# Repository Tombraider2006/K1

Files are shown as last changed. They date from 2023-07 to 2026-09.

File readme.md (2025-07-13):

<h3 align="right"><a href="https://www.tinkoff.ru/rm/yakovleva.irina203/51ZSr71845" target="_blank">ваше "спасибо" автору</a></h3>
<h3 align="right"><a href="https://t.me/tombraider2006" target="_blank">телеграм канал автора</a></h3>

[**Обучение в режиме онлайн консультации**](kurs.md)

[**дополнительные материалы к лекциям**](/extras/readme.md)

<h5 align="right">поставьте "звездочку" проекту. так другим пользователям легче его найти.</h5>

<h2>А я вам сейчас покажу откуда...</h2>

[**Актуальная версия прошивки с инструкциями по установке**](/version_config/readme.md) начинайте читать отсюда.

[**Обзор и быстрый старт прошивки Simple Af.**](/version_config/SimpleAF.md) Продвинутый вариант прошивки, Для этого варианта необходимо докупить датчик по Z.

[**Разное полезное про меню Helper Script**](/random/menu.md) то чего не написали нигде...

[**Родные коды ошибок креалити K1C**](https://store.creality.com/blogs/all/creality-k1c-fault-codes) по мне бесполезная шляпа, гораздо правильнее читать сообщения от клиппера в вебпанели. но если очень хочется можно и почитать. 

[**Родные коды ошибок креалити K1MAX**](https://store.creality.com/blogs/all/creality-k1-max-fault-codes-list) по мне бесполезная шляпа, гораздо правильнее читать сообщения от клиппера в вебпанели. но если очень хочется можно и почитать. 

[**Читаем графики шейперов**](/shaper/readme.md) Быстро разбираемся с графиками шейперов.

[**Регулировка натяжения ремней опираясь на графики**](/random/belts/readme.md) Разбираемся с графиком натяжения ремней, не быстро...

<h2>Макросы</h2>

[**Полезные макросы**](/macros_helpfull/readme.md) упрощаем работу с макросами формируя отдельный раздел с теми которыми будем пользоваться.

[**Управляем ретрактом во время печати**](/retract/readme.md) На коленке сляпанная инструкция далеко не всем нужная. 

[**Еще несколько советов по принтеру**](/ferma/readme.md) Разные полезные мелочи которые могут быть полезны при организации процесса печати.

[**таймер отложенной печати**](/random/timer.md) частный случай, однако пока его делал  нашел один интересный файлик который потом стал частью хелпер скрипта. 

[**Пропуск самопроверки после сброса до заводских настроек**](/random/reset.md)

<h2>Моды</h2>

[**Что купить чтобы принтер вас любил**](/what_2_buy/readme.md) статья в процессе правок

[**Актуальные печатные модификации**](https://t.me/crealityK1rus/16778) так как все течет все меняется, самые актуальные модели в телеграмм группе. 

[**Замена сопла Unicorn на Volcano в Creality K1\k1c\k1max**](https://3dtoday.ru/blogs/dimix200612/zamena-sopla-unicorn-na-volcano-v-creality-k1) при печати твердыми пластиками вполне неплохой выход удешевления затрат на сопла.

[**Установка стекла на стол для исправления кривизны**](https://www.youtube.com/watch?v=6vU0u630IjU&t=867s&ab_channel=ZeroDotCMD) видео на ютубе от зарубежного блогера, автоперевод субтитров вам в помощь 

[**Как поправить исправить наклон стола быстро**](https://www.youtube.com/watch?v=S2d_9Ysz-Q8&ab_channel=ZeroDotCMD) видео на ютубе от зарубежного блогера, автоперевод субтитров вам в помощь 

<h2>ОчУмелые Ручки</h2> Моды не всем нужные и на свой страх и риск.

[**Зачем нам одноплатник?**](/random/pi.md) различные модули которые не могут встать на родную операционную систему однако можно поставить на сторонний сервер **Spoolman**, **Telegram Bot**, **Klipperscreen**

<details><summary> <b>Активная термокамера. Cборник мануалов</b> </summary>

1. [**Подключение нагревателя камеры принтера**](/random/heater_chamber/readme.md) Если вы печатаете АBC и им подобными пластиками вам это пригодится.

2. [**Установка активного нагревателя термокамеры**](https://docs.idryer.org/iHeater/README_ru/) универсальнее стороннее решение с легкой установкой в любой принтер на клиппер.

3. [**Продвинутый вариант термокамеры с использованием дополнительного mcu**](https://github.com/artem-sedykh/K1C-chamber-heater)

</details>

<p>

[**Установка хотенда от Creality K2 Plus на Creality K1/c/max/se**](https://telegra.ph/Ustanovka-hotenda-ot-Creality-K2-Plus-na-Creality-K1cmaxse-05-13-2) Установка хотенда от K2 может понадобиться, если вы хотите увеличить максимальный объёмный расход на вашем принтере.

[**Подключение Raspberry Pico для расширения количества pin для ваших самоделок и дополнений**](/usb/readme.md) также добавил несколько примеров использования например для того же SFS

[**Датчик филамента sfs 2.0 для k1c\k1\k1max**](/sfs/readme.md) когда у нас не просто датчик обрыва филамента, а еще с реакцией если филамент остановился. пробка\запутывание филамента\окончание катушки с загнутым филаментом.

[**FBP Mod**](https://github.com/tlace17/K1-Flanged-Bearing-Project) замена стоковых деталей портала на напечатанные. есть свои плюсы, но свою пряморукость нужно учитывать до старта работы над проектом.

[**Установка сетевого разъема RJ45 на К1\K1C**](/random/ethernet.md) требует навыков пайки. 

[**Руководство по установке WLED**](https://github.com/Gliptopolis/WLED_Klipper) если очень хочется сделать из принтера новогоднюю ёлку.

[**Описание custom_macro.py**](/random/custom_macro.md) когда купил к1 думая что там обычный и клиппер и теперь сидишь и ничего не понимаешь.

[**Распиновка плат принтера**](https://docs.google.com/presentation/d/1f6kJbMq7uSggC33zmIfcTPdG6r50PbbDut14u9vAcZA/edit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) Энтузиастам.

[**выбор самурая - переход на клиппер без креалити**](https://github.com/pellcorp/creality/wiki/K1-Stock-Mainboard-Less-Creality)

[**Cartographer 3D. Если переходить на чистый клиппер придется уходить с родного модуля тензодатчиков.**](https://docs.cartographer3d.com/cartographer-probe/installation-and-setup/creality-k1-and-k1-max-specific)

[**Установка Creality K1 BTT Eddy**](https://ballaswag.github.io/blog/creality-k1-btt-eddy-guide/) буду ставить себе.. потом распишу подробнее.

[**модель держателя BTT Eddy с соединением в разьем лидара**](https://www.printables.com/model/1040464-btteddy-creality-k1-k1c-k1-max-mount)

[**Подключение одноплатника OrangePi (или любого другого) к K1.**](https://github.com/Lukich86/K1-host-conversion)

[**выбор самурая - ставим другую материнку, на примере MANTA 8**](https://docs.google.com/document/d/1aXhsg2oq-k43R_2uWEkFxx4bUmE72XdTxru3hAUbRM0/edit?tab=t.0)

[**обновленный тензомод**](https://github.com/Sekilsgs2/creality_pellcorp) где автоматизированный скрипт сам все поставит , очистит от хлама creality и поставит последний klipper  и можно юзать. Не как в tenso_mod - поставил и пол дня настраивай переделывай чтобы вообще хоть что то работало

[**Установка кулера модели от Пылесоса Roborock**](https://telegra.ph/Podklyuchenie-ventilyatora-Roborock-syaososa-k-3d-printeram-linejki-K1-06-06) Установка "Сяососа" может понадобиться, если вы часто печатаете Pla, Tpu и др. материалами, требующими активного охлаждения. Вентилятор Roborock может быстрее охлаждать слой, нежели улитка 5015 или 4020, что позволяет печатать быстрее на участках с маленькой площадью слоя 

[**Добавление функционала на основе virtual_pins на примере отключения вентиляторов в конце печати.**](/random/pins.md) исключительно как пример ну и тем кому это надо.(сами себе злобные буратино. я предупредил.)

[**CREALITY K1 FAQ перед первым включением.**](/random/before_use.md) **устарело** если вам попался этот пункт до того как вы вскрыли принтер вполне возможно что вы избежите перекоса стола

**как быстро определить какое сопло(unicorn\volcano) на вашем принтере**

если видно отверстие на радиаторе хотенда и болтик под шестигранник значит у вас vulcano, если радиатор без отверстий значит unicorn.

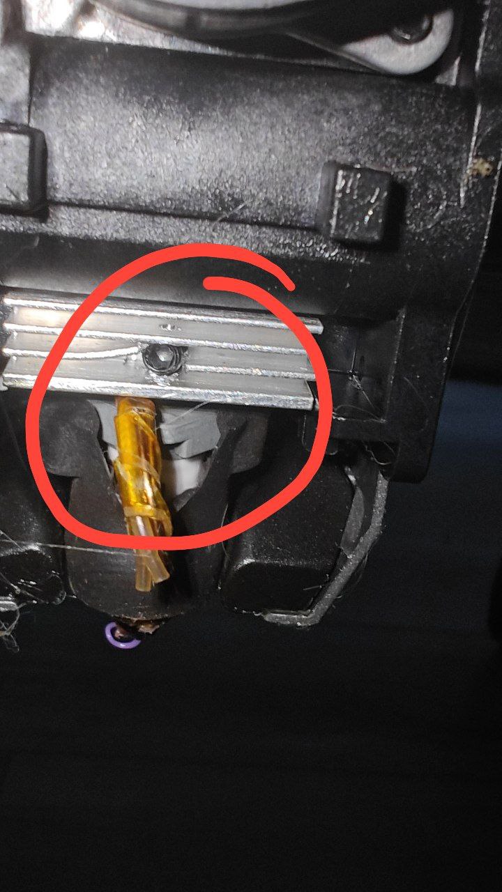
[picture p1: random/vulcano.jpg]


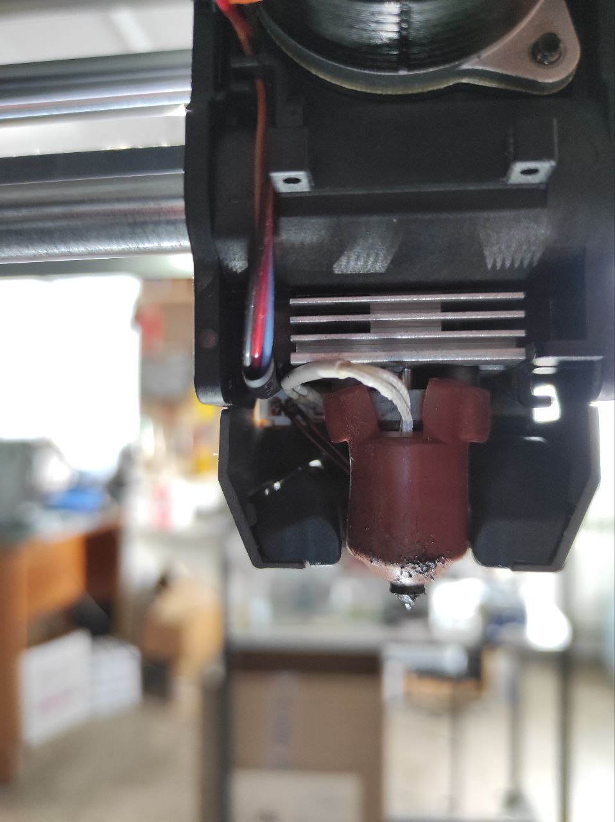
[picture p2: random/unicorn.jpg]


[**Ветка бутлоадера от CREALITY**](https://github.com/CrealityOfficial/K1_Series_Annex/releases/tag/V1.0.0)

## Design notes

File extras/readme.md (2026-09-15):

[↩️ Назад в главное меню](../readme.md)

---

# 📚 Дополнительные материалы к лекциям

> Полезные модели для печати, руководства по калибровке и видео-материалы

<h3 align="right"><a href="https://www.tinkoff.ru/rm/yakovleva.irina203/51ZSr71845" target="_blank">💝 Поддержать автора</a></h3>

---

## 📑 Оглавление

- [🔧 Печатные модели](#-печатные-модели)
- [🛠️ Устранение проблем со столом](#️-устранение-проблем-со-столом)
- [📊 Шейперы и калибровка](#-шейперы-и-калибровка)
- [🎯 Калибровка филамента](#-калибровка-филамента)
- [🎬 Видео-материалы](#-видео-материалы)
- [💧 Влажность пластика](#-влажность-пластика)
- [🛒 Расходные материалы](#-расходные-материалы)
- [⚙️ Adaptive PA](#️-adaptive-pa)

---

## 🔧 Печатные модели

### 1. Прокладка под экран

Уменьшает приток холодного воздуха в камеру принтера:

- **[K1 MAX](https://www.printables.com/model/553930-creality-k1-max-door-cover)**
- **[K1 / K1C](https://t.me/crealityK1rus/16778/293569)**

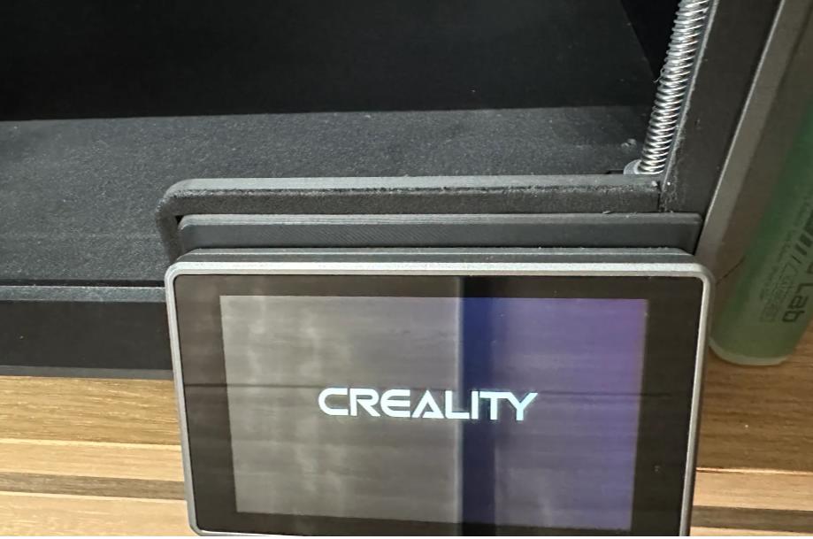
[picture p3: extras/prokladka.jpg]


### 2. Проставка для вентиляции

Устанавливается между корпусом и крышкой для улучшения воздухообмена:

- **[K1 / K1C](https://www.printables.com/model/525295-jc-creality-k1-hinged-lid-riser)**
- **[K1 MAX](https://t.me/crealityK1rus/16778/109114)**

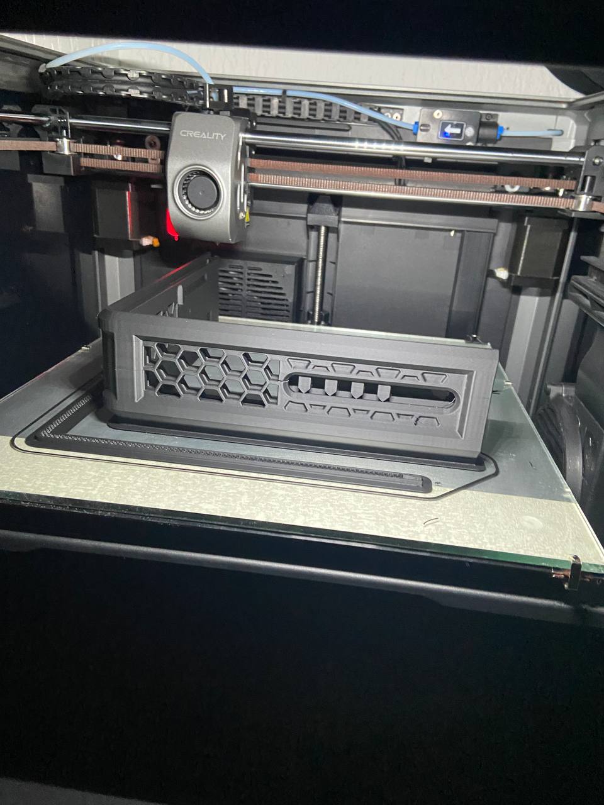
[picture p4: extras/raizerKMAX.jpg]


### 3. Держатель резинки прочистки

- **[Для K1C](https://t.me/crealityK1rus/16778/217607)**

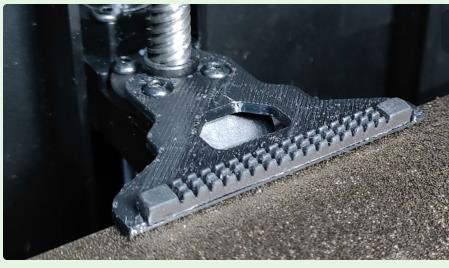
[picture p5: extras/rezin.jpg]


### 4. Тестовый кубик

**[Скачать обычный тестовый кубик](Cube.stl)**

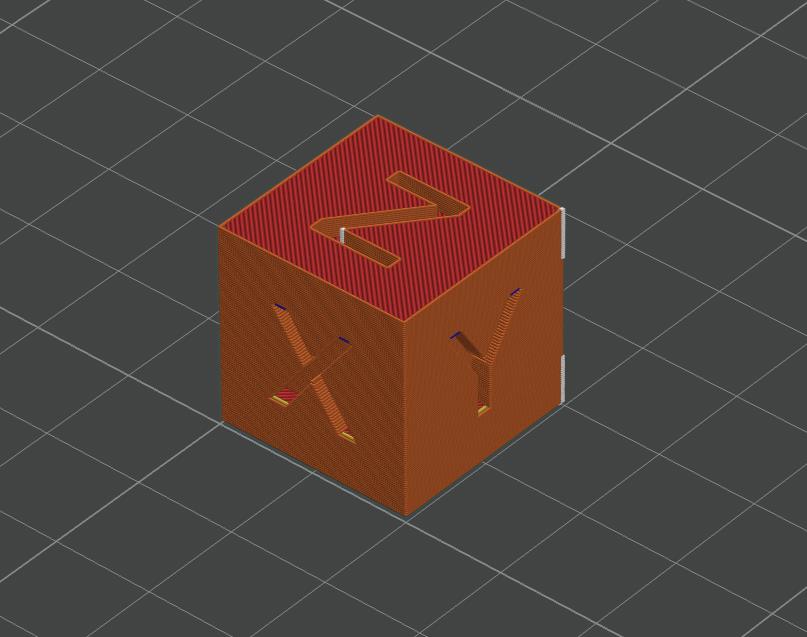
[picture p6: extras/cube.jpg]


---

## 🛠️ Устранение проблем со столом

### Методы исправления кривизны:

1. **[Установка стекла для исправления кривизны](https://www.youtube.com/watch?v=6vU0u630IjU&t=867s&ab_channel=ZeroDotCMD)** - видео на YouTube (англ.) | [Видео в чате K1](https://t.me/crealityK1rus/9504/602859)

2. **[Быстрое исправление наклона стола](https://www.youtube.com/watch?v=S2d_9Ysz-Q8&ab_channel=ZeroDotCMD)** - видео на YouTube (англ.)

3. **[Видеопояснение от пользователей](https://t.me/crealityK1rus/152020/451660)** - на русском в Telegram

---

## 📊 Шейперы и калибровка

### Что такое шейперы:

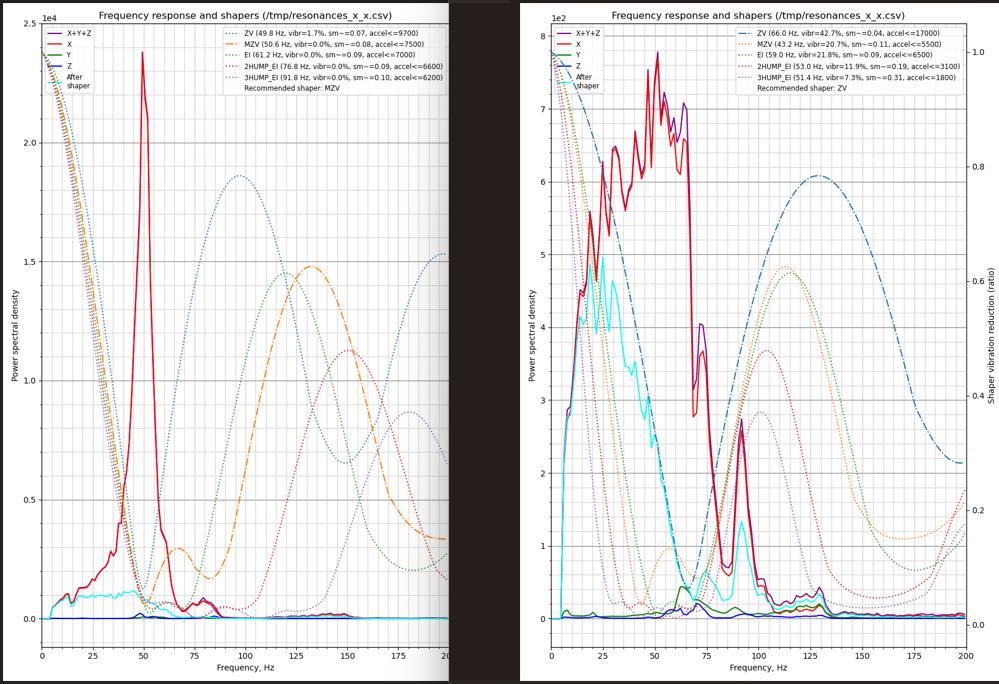
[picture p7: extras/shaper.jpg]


**Подробные материалы:**
- **[Материал на русском](https://github.com/Tombraider2006/klipperFB6/tree/main/accel_graph)** - подробная статья
- **[Материал на английском](https://github.com/Frix-x/klippain-shaketune/blob/main/docs/macros/axes_shaper_calibrations.md)** - от разработчиков
- **[Как понять графики шейперов](/shaper/readme.md)** - анализ графиков для K1 серии
- **[Регулировка натяжения ремней](/random/belts/readme.md)** - по графикам
- **[Helper Script меню](/random/menu.md)** - полезные функции

---

## 🎯 Калибровка филамента

### Порядок калибровки:

1. **Поток** (Экструзия)
2. **[Linear Advance](https://k3d.tech/calibrations/la/calibrator/)** (Pressure Advance)
3. **[Тест откатов](https://k3d.tech/calibrations/retractions/calibrator/)** (Retraction)
4. **Температура**
5. **Максимальная объемная скорость**

### G-коды для тестов Соркина:

⚠️ **Важно:** Используйте эти коды при калибровке PA и ретрактов

**Стартовый код:**
```gcode
_FULL_BED_MESH_ON
_ADAPTIVE_PURGE_LINE_OFF
START_PRINT EXTRUDER_TEMP=$HOTTEMP BED_TEMP=$BEDTEMP
```

**Конечный код:**
```gcode
SET_PIN PIN=FULL_BED_MESH VALUE=0
_ADAPTIVE_PURGE_LINE_ON
END_PRINT
```

---

## 🎬 Видео-материалы

### Слайсеры и настройка:

- **[Почему OrcaSlicer](https://youtu.be/0TzEFStKH90?si=3XKylqedC36pHxEK)** - обзор слайсера
- **[OrcaSlicer - Установка, Настройка, Работа](https://youtu.be/LeLj5oCacak?si=SBsEC19GKPhX8TuF)** - полное руководство
- **[Калибровка точности в OrcaSlicer](https://youtu.be/xzC4Fdf7mDU?si=dvUSbCUAnS6y5BpE)**
- **[Калибровки пластика 2026](https://youtu.be/_Sd-_t1A5_A?si=iGwRLs2JWSr-kxba)**
- **[Частые ошибки настройки 3D принтеров](https://youtu.be/3qv3-SMg5xY?si=traAK1FHAlSTLU77)**

### Материалы и калибровка:

- **[Все о филаментах](https://www.youtube.com/watch?v=CzgOCkJbcxE)** - подробный обзор
- **[Калибровка точности по Соркину](https://youtu.be/6seFEWIGTtU?si=9I6r6bh5QEWTt1Us)**
- **[Диаметр сопла: 0,4 vs 0,6](https://youtu.be/sNIYDhxbMe4?si=B41wK4Hl-1oPrVQ_)** - производительность

### 3D моделирование:

- **[Приемы моделирования для 3D печати](https://youtu.be/64Ce6Of0N2Q?si=uoQyqhyEkVIPD1hb)**

---

## 💧 Влажность пластика

### Как определить влажность:

Пользователь сфотографировал полоски Line Purge от KAMP - видны дефекты от влажного пластика:

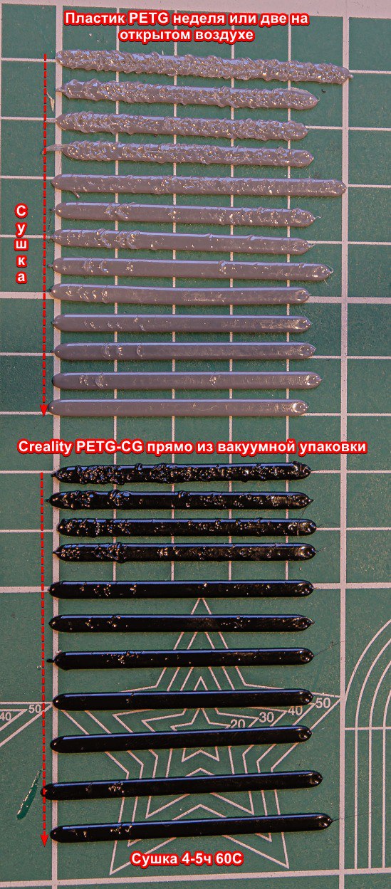
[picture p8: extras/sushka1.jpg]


⚠️ **Важно:** Даже пластик Creality в вакуумной упаковке с силикагелем может быть влажным!

**Рекомендации по сушке от Creality:**

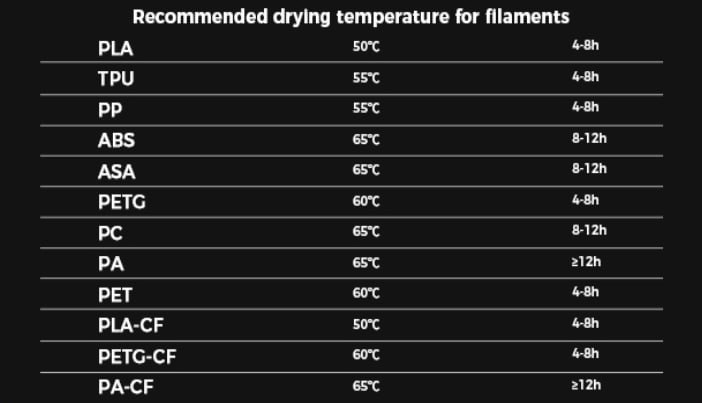
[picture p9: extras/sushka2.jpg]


---

## 🛒 Расходные материалы

### Расходные жидкости:

- Клей для FDM 3D печати
- Смазка для 3D принтеров
- Композитные полимерные материалы для 3D печати
- Матирующие спреи для 3D сканирования

**Где купить:** Через бот **@ATECOBot** или штучно на Ozon. Через бота - накопительная скидка | [Официальная группа](https://t.me/atecoru)

### Рекомендуемые пластики:

- **ABS** - [hi-tech-plast](https://www.ozon.ru/category/plastik-dlya-3d-printera-15794/hi-tech-plast-87286623/)
- **PETG** - [mako](https://www.ozon.ru/brand/mako-100524697/)
- **PLA** - [Eryone](https://www.ozon.ru/category/plastik-dlya-3d-printera-15794/eryone-100430904/)

---

## ⚙️ Adaptive PA

### Что это и зачем?

Разработчики OrcaSlicer решают проблему Pressure Advance на мостах и нависаниях.

**Проблема:** На мостах откалиброванный PA неприменим - сопло быстро теряет давление при экструзии в воздух. При возврате на стенку требуется время для восстановления давления → появляется полоса после моста.

**Решение:** Две новые функции:
1. **PA Bridge Override** - отдельная настройка PA для мостов
2. **Adaptive PA** - автоматическое изменение PA при изменении объемного потока

**В Klipper:** Решается проблема "PA change stutter" - дефекты на стенках при выходе из нависаний

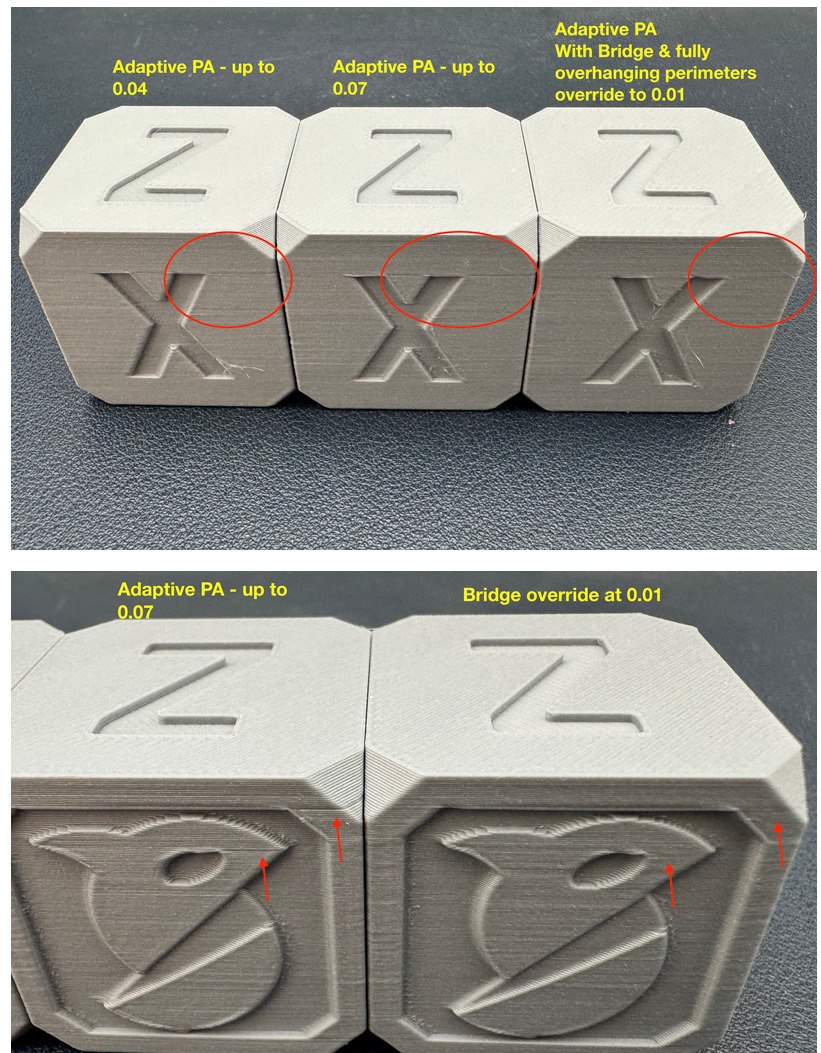
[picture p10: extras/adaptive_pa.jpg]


---

<div align="center">

**[↩️ Вернуться в главное меню](../readme.md)**

</div>

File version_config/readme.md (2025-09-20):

<h3 align="right"><a href="https://www.tinkoff.ru/rm/yakovleva.irina203/51ZSr71845" target="_blank">ваше "спасибо" автору</a></h3>
<h3 align="right"><a href="https://t.me/tombraider2006" target="_blank">телеграм канал автора</a></h3>

  <h1>Инструкция к прошивке 1.3.3.46</h1>

*Ремарка: Наибольшая функциональность на данной момент реализована на прошивке [**SimpleAF**](/version_config/SimpleAF.md) - не подходит для Sfc kit*
 
1. **рекомендую** если у вас были ранее установлены скрипты перед установкой сбросить прошивку до заводских настроек для исключения накладок.

   сначала ставим   [**HELPER SCRIPT**](https://guilouz.github.io/Creality-Helper-Script-Wiki/helper-script/helper-script-installation/) рекомендованные пункты:

      1, 2, 4, 5, 6, 7, 8, 9, 10, 11, 12, 16

      **для k1se**  1, 2, 4, 5, 6, 10, 11, 12 (нет бокового и заднего вентилятора, нет видеокамеры, нет бипера)
     
      **для Sfc kit** 1, 2, 4, 5, 7, 8, 9, 10, 11, 12, 16 (конфликт в макросах старта печати с модулем KAMP)
   
      прочитать про каждый из пунктов можно [**тут**](/random/menu.md)

3.  перезагружаем принтер по питанию. все работает. 

4. если у вас установлена камера- в настройках fluidd - камеры - добавить - пишем любое имя - жмем ок. переходим а настройки интервальной сьемки - выбираем нашу камеру. 

<h3>Баги установки</h3>
   
   Если во время установки moonraker начинает ругаться на сертификат,  перед установкой скрипта поставьте свой часовой пояс а потом обновите время - `hwclock -w` .
   
   проверить правильность даты и времени можно проверить командой `date`

   Недавно выявлен еще один баг. На команду клонирования с гита появляется ответ `error: Couldn't resolve proxy` Лечится командой:

   ```
   git config --global --unset http.proxy
   ```

### для установки хелпер скрипт на k1 с обновлением для CFS на прошивке 2.3.5.33

по ssh вставляем следующие команды: 

```
wget http://bin.entware.net/mipselsf-k3.4/installer/generic.sh -O - | sh
export PATH=/opt/bin:/opt/sbin:$PATH
echo '/opt/etc/init.d/rc.unslung start' >> /etc/rc.local; echo 'exit 0' >> /etc/rc.local
opkg update
opkg install git-http
# opkg install git  # (если предыдущая команда выдала ошибку)
git clone --depth 1 https://github.com/Guilouz/Creality-Helper-Script.git /usr/data/helper-script
mv /usr/bin/git /usr/bin/git.bak
ln -s /opt/bin/git /usr/bin/git
git config --global --add safe.directory /usr/data/moonraker/moonraker

```
после запускаем helper script:

```
sh /usr/data/helper-script/helper.sh
```

<h2>калибровки после установки.</h2>
 
 про полезные макросы читаем [**тут**](/macros_helpfull/readme.md)

 про калибровки шейперов читаем [**тут**](/shaper/readme.md)

 про калибровки ремней читаем [**тут**](/random/belts/readme.md)

**Для калибровок соркина на откаты и ЛА\ПА нужны такие стартовые и конечные коды**

стартовый код
```
_FULL_BED_MESH_ON
_ADAPTIVE_PURGE_LINE_OFF
START_PRINT EXTRUDER_TEMP=$HOTTEMP BED_TEMP=$BEDTEMP

```

конечный код

```
SET_PIN PIN=FULL_BED_MESH VALUE=0
_ADAPTIVE_PURGE_LINE_ON
END_PRINT

```

пройти тесты можно [**ТУТ**](https://k3d.tech/calibrations/)

<h2>что вы получите?</h2>

  флюид и мунрейкер - (отправка на печать из любого слайсера по wifi), таймлапсы, бипер в конце печати при паузе и при сработке датчика обрыва филамента, добавлены графики шейперов, натяжки ремней, сохраняется зет офсет при перезагрузке, тест на определенной частоте для определения резонируещих частей принтера , изменена логика кулеров, адаптивная сетка стола теперь с правильным макросом старта печати - если нет исключения обьектов будет рисовать боковую линию прочистки стандартную. также добавлен макрос *screws calibration* если вы решите использовать модификацию с барашками стола для их полуавтоматической настройки.  

ОБЯЗАТЕЛЬНО!!! провести тесты  шейперов и  PID экструдера!!!

**Если установили таймлапс, не забудьте прописать его в настройках орки**

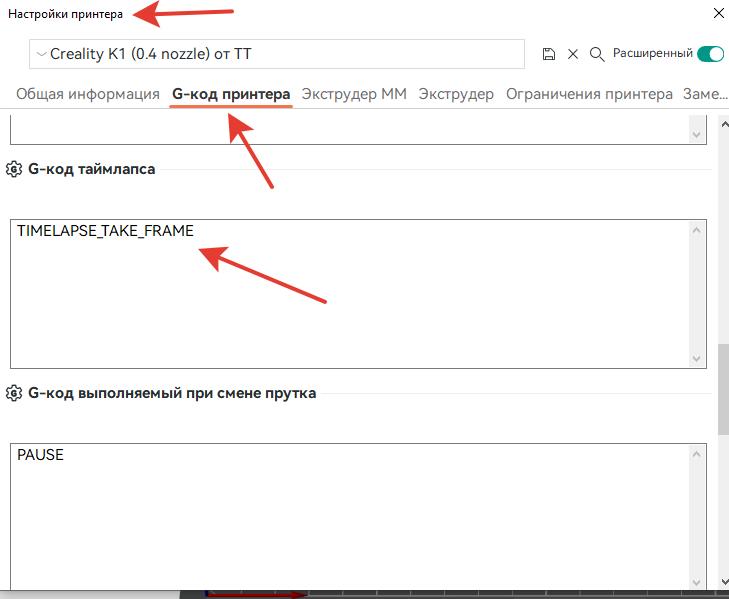
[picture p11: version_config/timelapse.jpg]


```
TIMELAPSE_TAKE_FRAME
```

**если возникает проблема с загрузкой Fluid или Mainsail** необходимо доустонавить еще компонент 

```
opkg install wget-ssl
```

мой выбор программы доступа по ssh  из  windows это: [**Bitvise SSH Client**](https://www.bitvise.com/ssh-client-download)

**чтобы после каждой печати  вас не раздражала надпись "сохранить настройки и перегрузить"**

 можно выполнить три простых пункта. зайти в настройки перейти в общие и добавить исключения. `bed_mesh adaptive` и `bed_mesh default`

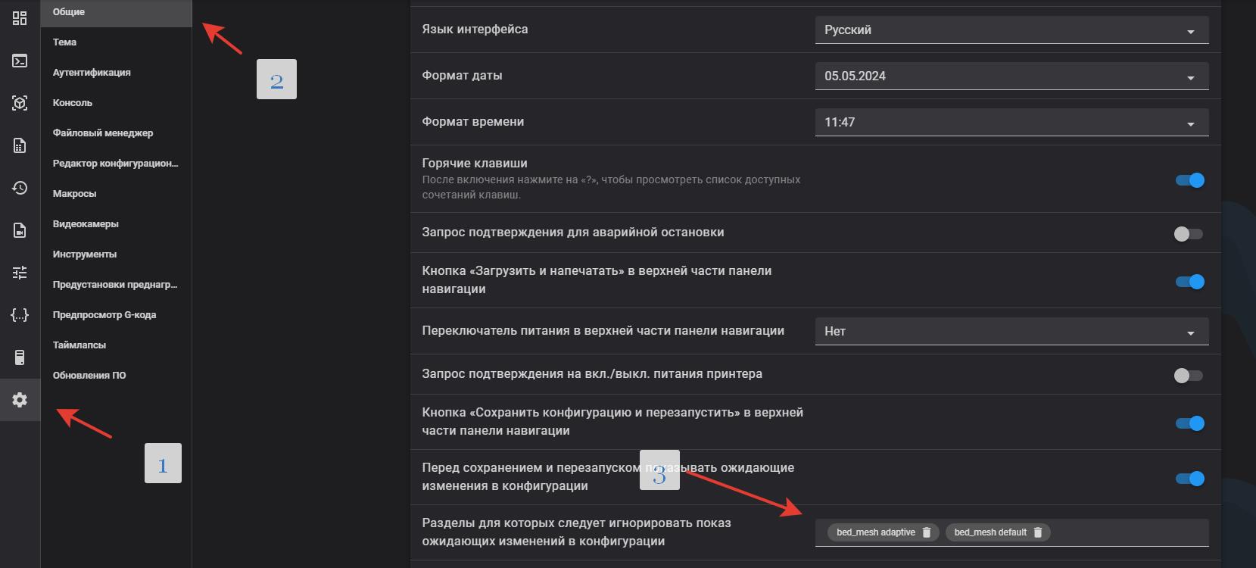
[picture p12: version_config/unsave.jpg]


**Небольшое замечание касательно KAMP.**

Он включает в себя две функции - адаптивную карту стола и макрос линии прочистки сопла.
Адаптивная карта стола не совместима с несколькими функциями, требующим построения полной карты стола.
В их число входит калибровка PA при помощи лидара и штатная линия прочистки сопла на левом краю стола, которая включается если отключена адаптивная линия прочистки из KAMP. Ни в коем случае не отключайте линию прочистки, если у вас включена адаптивная карта стола - это может привести к повреждению покрытия стола (хотя куда более вероятно простое налипание пластика на сопло из-за того, что оно слишком далеко от стола).

Точность калибровки лидаром также подвергается сомнению, вследствие чего чаще всего его рекомендуется просто отключить (вплоть до физического удаления с печатной головки принтера).

Также, если у вас используется мультиматериальная система (ERCF, TradRack, MMU, CFS и им подобные) - обратите внимание, что башня очистки не получает своего названия объекта и из-за этого на неё не распространяется область построения карты стола - пожалуйста, планируйте её размещение так, чтобы она попадала между другими объектами 

### Новый алгоритм измерения Input Shaping

Прочитать про отличия нового от старого алгоритма можно [**тут**](https://klipper.discourse.group/t/a-bit-different-resonance-test/17227)

### автоматический скрипт

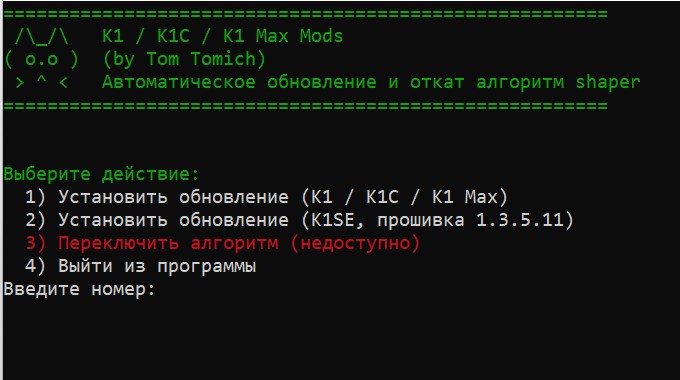
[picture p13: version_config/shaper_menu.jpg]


запускаем строчку в консоли ssh выбираем пункт. после установки произойдет перезагрузка принтера для применения настроек. всё. 

```
wget --no-check-certificate -O /tmp/shaper.sh https://raw.githubusercontent.com/Tombraider2006/K1/refs/heads/main/random/shaper.sh && chmod +x /tmp/shaper.sh && sh /tmp/shaper.sh

```

<details><summary>ручной способ</summary>
Чтобы его применить заходим по ssh и копируем следующий блок:

```
cd /usr/share/klipper/klippy/
mv toolhead.py toolhead.py.bak
rm toolhead.pyc
wget -P /usr/share/klipper/klippy/ https://raw.githubusercontent.com/Konstant-3d/K1C-mods/refs/heads/main/usr/share/klipper/klippy/toolhead.py
chmod 644 toolhead.py
cd /usr/share/klipper/klippy/extras/
mv resonance_tester.py resonance_tester.py.bak
mv shaper_calibrate.py shaper_calibrate.py.bak
rm resonance_tester.pyc
rm shaper_calibrate.pyc
wget -P /usr/share/klipper/klippy/extras/ https://raw.githubusercontent.com/Konstant-3d/K1C-mods/refs/heads/main/usr/share/klipper/klippy/extras/resonance_tester.py
wget -P /usr/share/klipper/klippy/extras/ https://raw.githubusercontent.com/Konstant-3d/K1C-mods/refs/heads/main/usr/share/klipper/klippy/extras/shaper_calibrate.py
chmod 644 resonance_tester.py
chmod 644 shaper_calibrate.py
sed -i 's/accel_per_hz: 75/accel_per_hz: 60/' /usr/data/printer_data/config/printer.cfg
reboot
```
после введения данных команд принтер перезагрузится и у вас будет новый алгоритм

Если захотите вернуться к старому алгоритму потом:

в `printer.cfg` находим раздел [resonance_tester]

и вписываем параметр `sweeping_period: 0`

или просто в панели ssh вписываем следующий код:

```
cp /usr/data/printer_data/config/printer.cfg /usr/data/printer_data/config/printer.cfg.bak

sed -i '/resonance_tester/{
n
n
n
n
n
n
a\
sweeping_period: 0
}' /usr/data/printer_data/config/printer.cfg

```
если захотим и после этого вернуть к новому алгоритму 

```
cp /usr/data/printer_data/config/printer.cfg /usr/data/printer_data/config/printer.cfg.bak

sed -i '/resonance_tester/{
n
n
n
n
n
n
a\
sweeping_period: 1.2
}' /usr/data/printer_data/config/printer.cfg

```

или в файле printer.cfg находим значение параметра `sweeping_period: 0` меняем на `sweeping_period: 1.2`

**Для K1SE с прошивкой 1.3.5.11**
По неведомой причине для данной прошивки необходим немного другой файл. Решение уже найдено, чтобы его применить вам, и только вам!, на других прошивках и принтерах работать не будет, необходимо в консоль ssh дополнительно к основному скрипту, скопировать следующие команды:

```
cd /usr/share/klipper/klippy/
mv toolhead.py toolhead.py.bak1
wget -P /usr/share/klipper/klippy/ https://raw.githubusercontent.com/Konstant-3d/K1C-mods/refs/heads/main/usr/share/klipper/klippy/toolhead_1_3_5_11.py
mv toolhead_1_3_5_11.py toolhead.py
chmod 644 toolhead.py
reboot
```
после введения данных команд принтер перезагрузится и у вас будет новый алгоритм
</details>

#### Продолжая тему нового алгоритма.

С одной стороны он несомненно показывает более точные результаты  по компенсации резонанса, но сильно смазывает картину при диагностике  по моему мануалу определения "нужно ли лечить ось икс". 
Поэтому моя рекомендация: сначала смотрим график по старому алгоритму, лечим по необходимости, потом устанавливаем алгоритм новый и на его основе устанавливаем шейперы

### Guppy Screen update

Исправленная версия GuppyScreen:

1. Пересобраны шрифты, используется NotoSans-Medium, включено subpx-сглаживание, поддерживается кириллица.
2. Изменены значения экструда на экране Extrude, выставлены более удобные в реальной жизни значения.
3. Поправлено обрезание статуса файла нижними кнопками на панели Print.
4. Поправлен выпадающий список Display sleep в настройках Guppy.
5. В сборку попало исправление остатка прутка в Spoolman, а так же должны работать usb-флешки.

Установка скриптом из helper-script:

1. Открыть скрипт на редактирование `/usr/data/helper-script/files/guppy-screen/guppy-update.sh`
Найти строку `"$CURL" -s https://api.github.com/repos/ballaswag/guppyscreen/releases -o /tmp/guppy-releases.json` и исправить слово `ballaswag` на `neonman63`
2. Запустить скрипт `sh /usr/data/helper-script/files/guppy-screen/guppy-update.sh`

Установка обновления вручную:

1. Закинуть архив любым способом в каталог /usr/data, например:
```
wget 'https://github.com/neonman63/guppyscreen/releases/download/nightly/guppyscreen.tar.gz' -O /usr/data/guppyscreen.tar.gz
или
scp guppyscreen.tar.gz root@ip-printer:/usr/data/
tar -xvf /usr/data/guppyscreen.tar.gz -C /usr/data/guppyscreen/..
/etc/init.d/S99guppyscreen stop
killall -q guppyscreen
/etc/init.d/S99guppyscreen restart
rm -f /usr/data/guppyscreen.tar.gz
```
Enjoy!

 вот  [**конфиги посмотреть**](/version_config/1_3_3_36/) в комментариях в файлах printer.cfg и gcode_macro.cfg можно увидеть какие параметры я менял и прочитать зачем.
   *это конфиг для стокового к1 с заменой шкивов и моторов. (в printer.cfg указаны строки где и что менять в 4 местах при замене на 20-зубые шкивы)*

## Ошибка 3002. Для всех кто обновился не удалив хелпер скрипт. 

заходим по ssh  и пробуем 
```
/etc/init.d/S58factoryreset reset
```
После выполнения ваш принтер запустится со сбросом настроек до значений по умолчанию, сохранятся только пользовательские настройки и параметры подключения.

если не помогло и вылазит ошибка
```
echo "all" | nc -U /var/run/wipe.sock
```
После выполнения появится сообщение `ok`, и принтер перезагрузится, а настройки будут сброшены до значений по умолчанию.

Необходимо повторно подключить принтер к сети с помощью экранного интерфейса пользователя Settings→ Network tab.

после сброса включаем root и заново накатываем хелпер скрипт
```
git clone https://github.com/Guilouz/Creality-Helper-Script.git /usr/data/helper-script
```
И введите эту команду для запуска скрипта:
```
sh /usr/data/helper-script/helper.sh
```

###  порядок установки если вам нужен более новый клиппер(устарело)

  Действия, которые нужно сделать:

1. Сбросьте настройки до заводских результатов
2. Убедитесь, что у вас установлена последняя версия прошивки
3.Получите права root на компьютере
4. Установите пакет Fluidd, Moonraker и менеджер Entware только с https://guilouz.github.io/Creality-Helper-Script-Wiki/
5. Обновите Klipper до более новой версии, следуя инструкции по адресу: https://github.com/K1-Klipper/installer_script_k1_and_max
6. Вернитесь и установите дополнительные вспомогательные скрипты с помощью установщика вспомогательных скриптов Guilouz
7. в printer.cfg найти раздел `[printer]` в нём удалить строчку  `max_accel_to_decel` и заменить эту строчку на `minimum_cruise_ratio: 0.5`
Это даст вам Klipper от **~8 апреля 2024.**

на данный момент проект приостановлен и врядли будет обновлятся далее. 

   <h5 align="right">поставьте "звездочку" проекту. так другим пользователям легче его найти.</h5>

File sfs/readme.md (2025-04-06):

<h3 align="right"><a href="https://www.tinkoff.ru/rm/yakovleva.irina203/51ZSr71845" target="_blank">ваше "спасибо" автору</a></h3>
<h3 align="right"><a href="https://t.me/tombraider2006" target="_blank">телеграм канал автора</a></h3>
<h5 align="right">поставьте "звездочку" проекту. так другим пользователям легче его найти.</h5>

<h1>Способ Номер 1</h1>
При печати на 3D принтере решил обезопасить себя не только паузой при окончании филамента, но также в случае перехлеста или другой причине остановки подачи пластика в экструдер  

Дляя этого был приобретен  датчик филамента ВТТ sfs v2.0

Решил припаяться к материнской плате. 

Так как короб с проводами вскрывать не хотелось, то отрезал контакты от купленного датчика с одной стороны (где их 2) просунул между проводами родного датчика и вытянул провода от родного датчика филамента, заодно протянув провода для нового. 

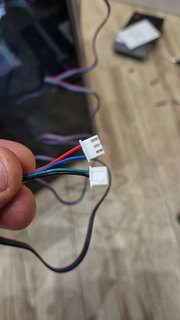
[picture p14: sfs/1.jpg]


*Вот это отрезал*

Далее берем SMD резистор 0402 на 100 ом (можно 0805)

Припаиваем резистор  сюда:

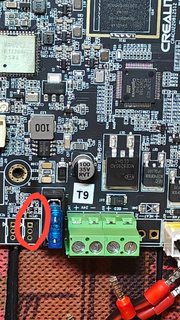
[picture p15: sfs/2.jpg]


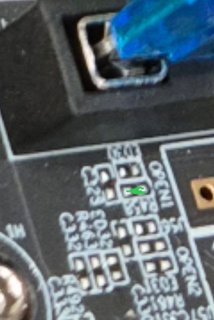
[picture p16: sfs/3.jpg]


*На этой фотографии видно лучше.*

Чтобы проверить правильность пайки - берем тестер и замеряем сопротивление - должно быть 100 Ом

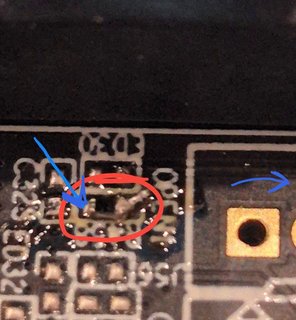
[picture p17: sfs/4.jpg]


Один щуп сюда, второй на дальнее отверстие разъема
Далее берем 3-пиновый разъём PH2.0 (можно и XH2.54 , но придется чуть подогнуть ножки)

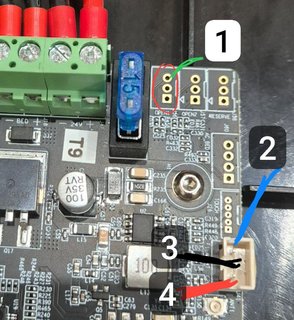
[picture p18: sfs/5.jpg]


Соединение делаем так - цвета линий соответствуют цвету проводов от датчика.

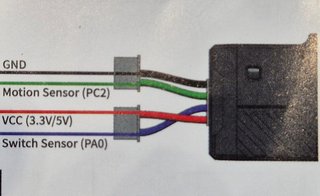
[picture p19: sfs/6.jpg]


Из инструкции
Для принтера на klipper и/или стоковой прошивке  вносим правки в `printer.cfg`

Надо закомментировать/удалить код, который прописан был для родного датчика и вписать следующий код:

```
[filament_switch_sensor filament_sensor]
switch_pin: ^PC15
pause_on_runout: False
runout_gcode:
 PAUSE # [pause_resume] is required in printer.cfg
 M117 filament_switch_runout
insert_gcode:
 M117 Filament switch inserted

[filament_motion_sensor encoder_sensor]
switch_pin: ^PA7
detection_length: 5.3
extruder: extruder
pause_on_runout: False
runout_gcode:
 PAUSE # [pause_resume] is required in printer.cfg
 M117 filament_encoder_runout
insert_gcode:
 M117 Filament encoder inserted

 ```
Перезагрузить прошивку и всё должно работать.

Можно поменять синий и зеленый провода местами, при этом не забудьте поменять пины в вышеуказанном коде. 

P.S. Про длину (detection_length) 

Параметр `detection_length: 5.3` 

отвечает за длину в мм за которое должен поступить сигнал от энкодера, если этого не происходит, то датчик дает сигнал о том, что нить перестала двигаться.

Производитель рекомендует поставить 2.88, но по факту подбора у меня перестали быть ложные срабатывания только на 5.3

P.S.S. **Про подтяжки**

В процессе тестирования выяснилось, что нужна подтяжка обоих сигнальных пинов к питанию. Есть 2 варианта - в конфиге перед именем пина дописать "^" (сейчас в коде выше так и указано), либо напаять внутрь SFS (место там есть) физические подтяжки из резисторов 10кОм. По совету сообщества пошел по второму пути, но будет работать и первый способ.

Для способа с резисторами в коде должно быть так:
```
[filament_switch_sensor filament_sensor]
switch_pin: PC15
```

```
[filament_motion_sensor encoder_sensor]
switch_pin: PA7
```

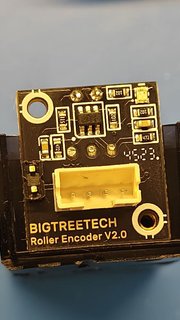
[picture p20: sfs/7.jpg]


Вид датчика с лицевой стороны

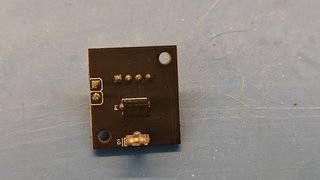
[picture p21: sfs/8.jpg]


С обратной стороны (еще без резисторов)

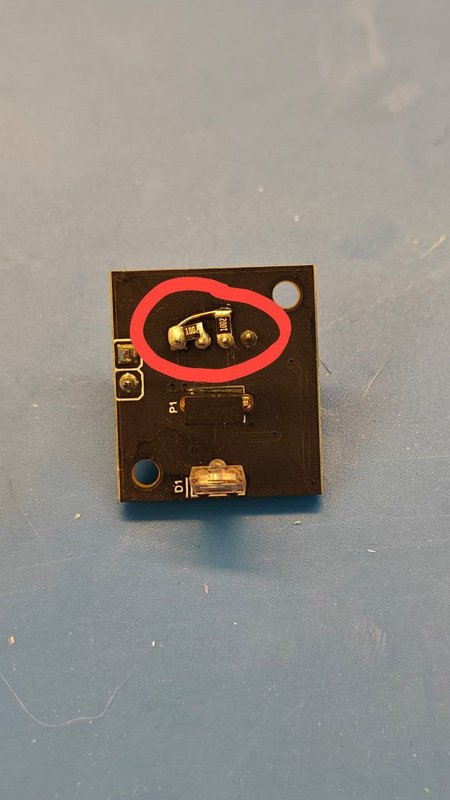
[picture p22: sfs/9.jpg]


результат

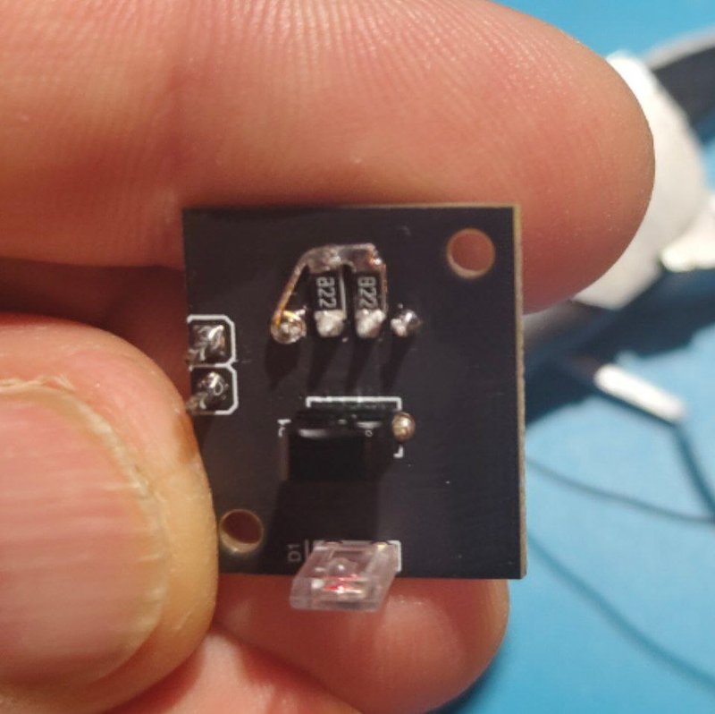
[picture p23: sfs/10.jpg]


Можно и так

[спасибо за мануал](https://telegra.ph/Datchik-filamenta-sfs-20-dlya-k1c-09-30)

<h1>Способ номер 2</h1>

в способе номер 2 мы будем использовать только штатную проводку, точнее, только датчик движения. Если нить заканчивается, то будет определено, что «не движется», и принтер встанет на паузу.
Вам не нужно лезть в материнскую плату, или куда либо еще, чтобы подключить новый датчик. Единственный отрицательной момент в том, что будет гореть иконка  "не вставлен филамент" на экранчике принтера так как мы сменили тип датчика но это будет раздражать только законченных пефекционистов, остальные рыжие 4на4 пикселя переживут.

Разводка по проводам следующая:

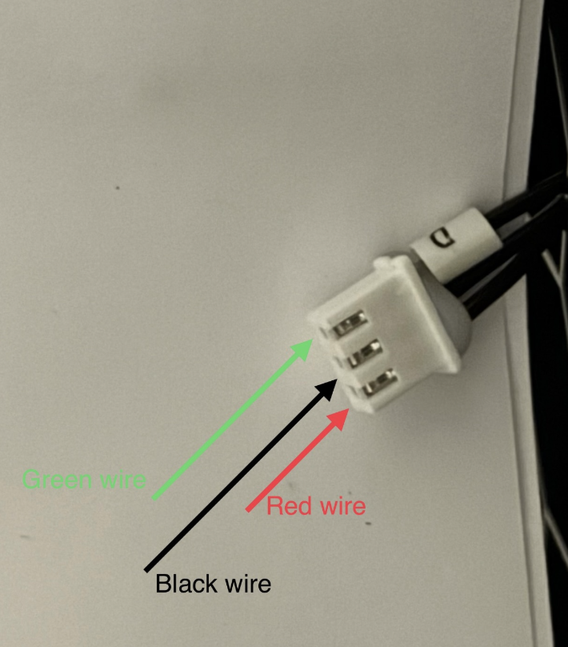
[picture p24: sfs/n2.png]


на материнской плате:

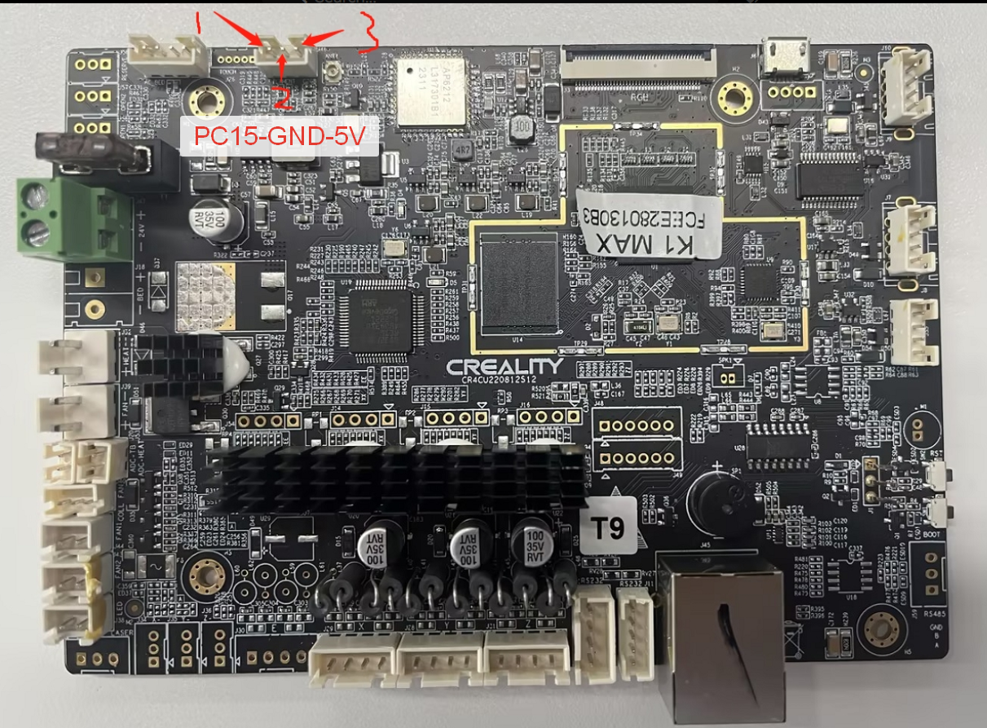
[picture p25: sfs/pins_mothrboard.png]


Далее заходим в `printer.cfg` и ищем строки:

```
[filament_switch_sensor filament_sensor]
pause_on_runout: true
switch_pin: !PC15
runout_gcode:
  {% if printer.extruder.can_extrude|lower == 'true' %}
    G91
    G0 E30 F600
    G90
  {% endif %}
```
эти строки стираем и вписываем вместо них:

```
[filament_motion_sensor filament_sensor]
detection_length: 5.3
extruder:extruder
pause_on_runout: true
switch_pin: ^PC15
runout_gcode:
  RESPOND TYPE=command MSG="Filament runout/blocked!"
  UPDATE_DELAYED_GCODE ID=sfs_alarm DURATION=1
insert_gcode:
  RESPOND TYPE=command MSG="Filament inserted"
  UPDATE_DELAYED_GCODE ID=sfs_alarm DURATION=0

[delayed_gcode sfs_alarm]
# initial_duration: 2
gcode:
  beep # звуковой сигнал если заканчивается филамент во время печати.
```

Строка с `beep` если у вас к1с вам не нужна, у вас нет пищалки. так же будет выдавать ошибку если вы не установили в своем принтере Buzzer Support через Helper Script.  Если у вас нет пищалки или вы не устанавливали - смотрите второй вариант кода ниже.

Мне тут не спалось и решил я что пользователям к1с как то обидно будет что нет у них никакой сигналки при паузе по движению поэтому немного переписал модуль чтобы моргал подсветкой 3 раза. Не супер, но хоть что то.

```
[filament_motion_sensor filament_sensor]
detection_length: 5.3
extruder:extruder
pause_on_runout: true
switch_pin: ^PC15
runout_gcode:
  RESPOND TYPE=command MSG="Filament runout/blocked!"
  UPDATE_DELAYED_GCODE ID=sfs_alarm DURATION=1
insert_gcode:
  RESPOND TYPE=command MSG="Filament inserted"
  UPDATE_DELAYED_GCODE ID=sfs_alarm DURATION=0
  SET_PIN PIN=LED VALUE=1

[delayed_gcode sfs_alarm]
# initial_duration: 0
gcode:
  SET_PIN PIN=LED VALUE=0
  G4 P500
  SET_PIN PIN=LED VALUE=1
  G4 P1000
  SET_PIN PIN=LED VALUE=0
  G4 P500
  SET_PIN PIN=LED VALUE=1
  G4 P1000
  SET_PIN PIN=LED VALUE=0
  G4 P500
  SET_PIN PIN=LED VALUE=1
  G4 P1000
```

модель для установки [скачать тут](BTT_SFS.zip) крепится штатными винтами из комплекта к креплению.

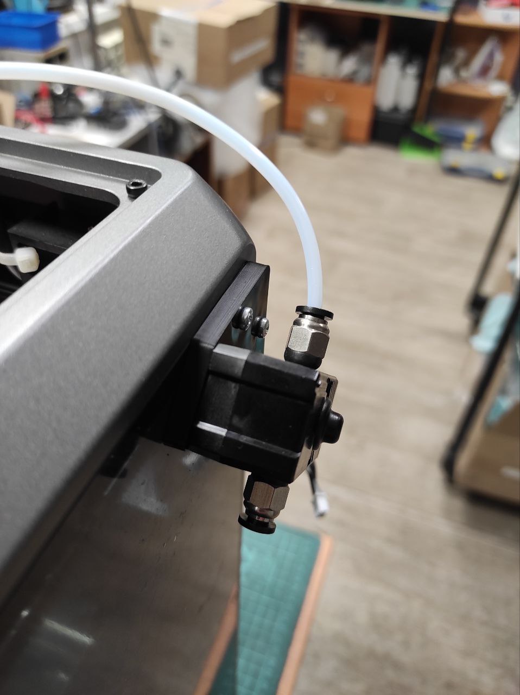
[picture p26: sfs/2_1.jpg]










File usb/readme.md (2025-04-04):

<h3 align="right"><a href="https://www.tinkoff.ru/rm/yakovleva.irina203/51ZSr71845" target="_blank">ваше "спасибо" автору</a></h3>
<h3 align="right"><a href="https://t.me/tombraider2006" target="_blank">телеграм канал автора</a></h3>

**Подключение raspbery pico к принтеру**

Основным препятствием в ваших самоделках может быть отсутствие свободных пинов на материнской плате принтера, данный мануал даст вам возможность добавить их некоторое количество с помощью подключения дополнительного mcu основанного на Raspbery pico. что даст возможность подключить множество различных устройств. 

Дополнительным плюсом данного решения является то что в случае форсмажора, в 90% случаев, сгорит плата за 500р которая не влияет на процесс печати. если искать пин на плате принтера - в случае форсмажора и  неисправности материнской платы траты в виде 5000р и простой принтера на время доставки платы.

**1.** Вскрываем днище нашего корпуса принтера.



**2.** Находим свободный юсб разъем на плате. *Свободный он у пользователей к1\к1с но и пользователям к1макс обычно он не нужен так как задействован под лидар который все  снимают*



**3.** Обжимаем разьем из любого подходящего микро юсб кабеля. Разъёмы на плате принтера для всех USB подключений - JST PH 2.0 mm 4pin (PH2.0 4P) *Тут сделаю небольшую ремарку, вывести кабель я предлагаю на заднюю стенку принтера, благо там есть и кабель каналы и отверстия подходящие,  Можно вывести не просто разьем microUSB а полноценный хаб на 2-4 разьема, его и проверить легче - определилась вставленная флешка - значит все соединено правильно.* 



**4.** Теперь нам нужно прошить нашу pico. На самом принтере "К1" серии это сделать проблематично поэтому есть несколько вариантов поставить klipper на другую подходящую железку

```
cd ~/klipper
make clean
make menuconfig
```

   в меню выбрать:



потом:

```
make
```

Переходим в каталог, в который скомпилировалась прошивка cd ~/klipper/out и смотрим там листинг файлов ls -la. Там должен быть файл с именем `klipper.uf2`

ну или не мучаться и скачать готовую прошивку [**тут**](klipper.zip) не забудьте распаковать файл. 

*чужой конфиг\прошивка - как чужие трусы. подойти может но послевкусие неприятное*

**5.** Прошиваем:

 UF2 режим можно активировать удерживанием кнопки BOOTSEL при подачи питания по USB. Появится накопитель «RPI-RP2», который можно использовать для копирования бинарных файлов uf2.

**6.** Подключаем к разьему.

Зайдя на наш принтер по ssh выполняем:

```
ls /dev/serial/by-path/* 
```
(также можно использовать /dev/serial/by-id/)

```
ls /dev/serial/by-id/*
```

должны увидеть что-то типа такого:(цифры буквы могут быть другими. важно что такое устройство определяется)

```
 /dev/serial/by-id/usb-Klipper_rp2040_E660B4404B3EAB35-if00
```

если не увидели то возможные варианты:

 - плохой кабель
 
 - неправильно сделан разьем.

**6.1** Предлагаю сразу распечатать корпус для нашей MCU чтобы не выглядело лютым колхозом.  [**модель тут**](https://www.printables.com/model/226610-raspberry-pi-pico-case/files)

**7.** В нашем printer.cfg в любом удобном месте добавляем строки:

```
[mcu pico]
serial: /dev/serial/by-id/usb-Klipper_rp2040_E660B4404B3EAB35-if00 # строку берем из пункта 6. свою.
```
где после `serial:` идет та  строка что мы получили в предыдущем пункте.

Теперь у нас все готово для добавления наших пинов в наши проекты. 



После прошивки и конфигруации MCU Raspberry Pico сразу предоставляют доступ к своим pin. Единственным условим их корректного использования будет четкое указание к какому Pin идет обращение, например, у нас есть MCU Pico
```
[mcu pico]
serial: /dev/serial/by-id/usb-Klipper_rp2040_E660B4404B3EAB35-if00
```

Обращение к его 'Pin' внутри конфигурационного файла будет выглядеть следующим образом:

```
pico:gpio1
```

<h1>FWS</h1>

Например - конфиг для датчика толщины филамента будет выглядеть так:

```
[hall_filament_width_sensor]
adc1: pico:gpio26
adc2: pico:gpio27
cal_dia1: 1.48
cal_dia2: 1.99
raw_dia1: 8750
raw_dia2: 9175
default_nominal_filament_diameter: 1.75
max_difference: 0.150
measurement_delay: 665
enable: True
logging: True
measurement_interval: 5
```
<h1>NEOPIXEL</h1>
Подключить светодиодную ленту можно например так:

```
[neopixel pico]
pin: pico:gpio16
#color_order: GRB
initial_GREEN: 0.5
```
На управляющий провод в цепь вставить резистор 200-500Ом, обьеденить GND питания ленты и платы. запитывать адресную ленту из расчета 0.2 ватта на 1 светодиод. 

Пример расчета: 

1. если у нас 100 светодиодов на 5 вольт то 100*0.2/5=4А тоесть нам нужна плата понижения напряжения с 24до 5 вольт на 4 ампера

2. если у нас 100 светодиодов на 12 вольт то 100*0.2/12=1.67А  тоесть нам нужна плата понижения напряжения с 24до 12 вольт на 2 ампера 

в обоих вариантах предполагается что источником питания ленты будет БП принтера через понижающее реле.



картинка про ардуино но суть та же. 

Я сразу поясню разницу. неопиксель через rpi дает возможность управлять лентой из клиппера, но там же придется и писать все эффекты. вариант с прошивкой WLED esp32 дает возможность делать ссылки на сохраненные в прошивке esp эффекты. если  смотреть на адресную ленту как на гирлянду, то предпочтительнее выглядит вариант esp32 если есть задумки использовать в конфиге ленту (например счетчик процентов печати в количестве светодиодов включенных) то rpi2040 выглядит интереснее.

<h1>Beeper</h1>

```
[gcode_macro M300]
gcode:
    # Use a default 1kHz tone if S is omitted.
    {% set S = params.S|default(1000)|int %}
    # Use a 10ms duration is P is omitted.
    {% set P = params.P|default(100)|int %}
    {% if S > 0 %}
      SET_PIN PIN=BEEPER VALUE=0.5 CYCLE_TIME={ 1.0/S }
      G4 P{P}
    {% else %}
      G4 P{P}
    {% endif %}
      SET_PIN PIN=BEEPER VALUE=0
```
макрос для реакций на команду м300 конвертнуть миди файлы в gcode можно [**тут**](https://www.layerfused.com/MIDI-M300) 

Не забываем поставить правильный пин куда воткнули наш *ПАССИВНЫЙ* бипер, иначе разницы в тонах не получим. 

```
[output_pin BEEPER]
pin: pico:gpio8
pwm: True
value: 0
shutdown_value: 0
cycle_time: 0.001
```

Вообще с пинами можно делать много чего например включать и выключать (подробно можно почитать в [klipper referense](https://github.com/Klipper3d/klipper/blob/master/docs/Config_Reference.md#output_pin)), снимать с них данные, даже управлять сервоприводом.

<h1>SERVO</h1>

```
[servo matrix]
pin: pico:gpio16 #  пин на плате
maximum_servo_angle: 180 # градус сервы
minimum_pulse_width: 0.0008 # по умолчанию 0.001 тут можно поиграться когда серва не поворачивается на полную
maximum_pulse_width: 0.0025 # по умолчанию 0.002 важно не только уменьшать но и увеличивать. тоесть играем парой значений одновременно
initial_angle: 0 # не меняем. это стартовый угол при загрузке принтера
```

Вид данных по типу смотрите по картинке подсказке выше. если вы пытаетесь подключить датчик i2s не стоит его пихать в обычный gpio тоже самое с данными spi.   

<h1>I2C</h1>
В следующих примерах придется поискать правильный адресс `i2c_bus: i2c2` может принимать вид от i2c0 до i2c4 но зато потом можно наслаждаться видом датчиков в вашей конфигурации

конфиги для датчиков(в любом месте вашего `printer.cfg`):

**BME280** [купить тут](https://alii.pub/6mct88)
```
[temperature_sensor Камера_принтера]
sensor_type: BME280
i2c_address: 118
i2c_bus: i2c2
```
**LM75A** [купить тут](https://alii.pub/6mct90)
```
[temperature_sensor LM75A]
sensor_type: LM75
i2c_address: 72
i2c_bus: i2c2
```

**HTU21D** [купить тут](https://alii.pub/6mctad)

```
[temperature_sensor HTU21D]
sensor_type: HTU21D
i2c_address: 64
i2c_bus: i2c2
```
После `temperature_sensor` можно вписать произвольное имя. как в первых примерах.

Также надо заметить что к одной шине SCL\SDA можно подключать несколько датчиков. На данный момент нет возможности проверить. согласно мануала подключаются они паралельно, но на всех датчиках кроме первого необходимо выпаять подтягивающие резисторы. 

P.S. Адреса i2c устройств прописываются жестко `i2c_address:`  вставить десятичный адресс, не HEX! 



<h5 align="right">поставьте "звездочку" проекту. так другим пользователям легче его найти.</h5>

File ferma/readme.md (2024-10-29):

<h3 align="right"><a href="https://www.tinkoff.ru/rm/yakovleva.irina203/51ZSr71845" target="_blank">ваше "спасибо" автору</a></h3>
<h3 align="right"><a href="https://t.me/tombraider2006" target="_blank">телеграм канал автора</a></h3>
<h5 align="right">поставьте "звездочку" проекту. так другим пользователям легче его найти.</h5>

**советы по организации фермы из принтеров creality K серии**

Организуя 3д ферму хочется упростить себе жизнь  и максимально облегчить управление принтерами. в первую очередь это создание одного файла  для возможности печати на разных принтерах.

мы будем рассматривать на примере слайсера орка. однако советы будут работать и на других современных слайсерах.

**0. установка модифицированного ПО**

Родная веб панель от Creality не имеет возможности доступа к файлам конфигурации и в принципе весьма бедна по фукционалу, поэтому прежде чем обсуждать остальные модификации  необходимо установить надстройку по [этому мануалу](/version_config/readme.md)

**1. регулируем шаги экструдера.**

   Важно понимать что если у вас 1 принтер вы можете игнорировать этот пункт и просто подогнать коофициент потока в вашем слайсере и это не будет какой то проблемой, однако если вы нарезаете один раз файл и отправите на разные принтеры с неотрегулированным шагом экструдера это может стать  причиной некачественной печати. все фидеры К серии суть один и тот же с небольшими нюансами.  один из самых простых способов проверки будет описан тут. итак открутим 3 винта на голове нашего принтера и снимем фидер вытащив его вверх.(не забудьте перед этим извлечь филамент) 




  
   1. В `printer.cfg` в конец раздела `[extruder]` добавим строку `min_extrude_temp: 0`  - это позволит выдавливать пруток без включения нагревателя. Строка временная, потом можно удалить.
   
   2. `rotation_distance: 6.9`  значение по умолчанию  используем как отправную точку для расчетов. 
     
   3. заправляем пруток, так чтобы он вышел наружу снизу и откусываем его вровень с корпусом.
   
   4. В консоли пишем :
   
```
    G91
    G1 E300 F60
```
Это выдавит 300 мм прутка на обычной скорости экструдера.(такой расчет достаточно точный и рекомендуемый но медленный)

   5. Берем свой rotation_distance = 6.9 и делю на 300 (столько я отправил прутка на продавливание) 
    получаю Х и это число умножаю на фактически вылезший пруток. Такой нехитрой формулой получаем свой `rotation_distance` идеальный именно для этого принтера. значение может колебаться в небольших пределах.

**2. настройка ретрактов**

подробное описание настроек есть в [**мануале**](/retract/readme.md)

**3. называем принтеры правильно. настраиваем цветовую схему**

В слайсере присваиваем каждому из принтеров порядковый номер.  можно распечатать номера и приклеить на каждый из принтеров и если их меньше 5 можно ввести цветовую индетификацию дополнительно в темах того же fluid  выбрав похожую. 





**4 Преднагрев камеры перед печатью**

в данном случае задача была максимально быстро нагнать необходимую температуру предварительно отогнав в угол голову.
я добавил еще опускание стола вниз для более полного прогрева.  по умолчанию стол в момент работы макроса нагревается до 100 градусов температура камеры целевая 42 градуса. данный макрос можно внести в слайсер в разделе стартового кода.

```
[gcode_macro chamber_hot]
description: hot temp in chamber
gcode:
  {% if printer.toolhead.homed_axes != "xyz" %}
    RESPOND TYPE=command MSG="Homing..."
    G28
  {% endif %}
  {% set POSITION_X = printer.configfile.settings['stepper_x'].position_min+10%}
  {% set POSITION_Y = printer.configfile.settings['stepper_y'].position_max-10%}
  {% set POSITION_Z = printer.configfile.settings['stepper_z'].position_max-10%}
  G1 X{POSITION_X} Y{POSITION_Y} F6000
  G1 Z{POSITION_Z}
  M84
  M106 P0 S200
  M106 P2 S80
  SET_TEMPERATURE_FAN_TARGET TEMPERATURE_FAN=chamber_fan TARGET={params.CHAMBER_TEMP|default(42)}
  M190 S{params.BED_TEMP|default(100)}

```
<h3>вариант 2.</h3>

для того чтобы не ждать набора температура в камере перед печатью но данные о температуре передавались  можно в профиле пластика добавить: 

```
M141 S{overall_chamber_temperature}
```
получится как то так (как оказалось нужен именно М141 а не М191 как указано на скриншоте)





на первый слоях теперетаура камеры не так важна, так как окружающие потоки воздуха от стола создают теплую рубашку, а к той высоте когда это становится критично уже наберется температура в камере. 

**5 Изменение количества точек теста стола - больше 36**

При попытке увеличить количество точек для более точной карты стола возникает непонятная ошибка, утверждающая, что увеличить количество точек невозможно

Для настройки bed_mesh требуется доступ к файлам конфигурации - см. выше. Обязательно сделайте резервную копию файла конфигурации перед внесением изменений!

A: Модуль prtouch, отвечающий за построение карты стола, жёстко ограничен 36 точками, для каждой из которых прописана калибровка граничных показателей веса. Однако, хоть и не рекомендуется так делать - можно отключить это ограничение, но для этого придётся сильно переписать раздел [prtouch_v2].
В первую очередь, нужно изменить поле pr_version на 1:

```
[prtouch_v2]
pr_version: 1
```

Затем, нужно удалить все строчки, начинающиеся на `tri_min_hold` и `tri_max_hold` - это строки с `tri_min_hold_1` до `tri_min_hold_36` и с `tri_max_hold_1` до `tri_max_hold_36` - это как раз параметры с ограничениями веса. Их легко найти по китайским иероглифам :D
С указанной версией 1 prtouch выведет их сам. Остальные строчки, сколько там их есть - оставьте как есть.

После этих изменений, можно в секции [bed_mesh] указать любой размер карты стола - например, для карты с 8*8 точек:

```
[bed_mesh]
algorithm: bicubic
probe_count: 8,8
```

**6 Настрока звуковых сигналов на к1\К1Макс(в к1с нет бипера как и в совсем новых к1\кмакс)**

Если вы при установке через хелпер скрипт установили `buzzer support`  то вам доступны следующие сценарии: 

1. звуковая сигнализация при окончании филамента. Для этого достаточно зайти в `printer.cfg` найти раздел `[filament_switch_sensor filament_sensor]`
и в конце раздела написать `beep` как на скриншоте ниже. или просто заменить раздел на это:

```
[filament_switch_sensor filament_sensor]
pause_on_runout: true
switch_pin: !PC15
runout_gcode:
  {% if printer.extruder.can_extrude|lower == 'true' %}
    G91
    G0 E30 F600
    G90
  {% endif %}
  beep
  beep
```



2. звуковая сигнализация при окончании печати. Идем в файл `gcode_macro.cfg`  и находим макрос `END_PRINT` меняя его следующим образом:

```
[gcode_macro END_PRINT]
gcode:
  Qmode_exit
  EXCLUDE_OBJECT_RESET
  PRINT_PREPARE_CLEAR
  M220 S100
  SET_VELOCITY_LIMIT ACCEL=5000 ACCEL_TO_DECEL=2500
  TURN_OFF_HEATERS
  M107 P1
  M107 P2
  END_PRINT_POINT
  beep
  WAIT_TEMP_START
  M84
```
если необходимо  подавать сигнал подольше, просто добавляем количество `beep` в макрос.

выдает звуковой сигнал при ошибках печати. работает не во всех случаях но работает.

```
[virtual_sdcard]
path: /usr/data/printer_data/gcodes
on_error_gcode: # добавляем чтоб пикало при ошибках
  beep
  beep
  beep

```

**7. Убираем раздражающие напоминания "сохранить и перегрузить" от временной карты стола** 

После печати принтер предлагает сохранить временную карту стола. Так как мы пользуемся KAMP которая делает карту только части стола для печати наших моделей это нам совсем не нужно.  заходим в настройки нашей вебпанели и в самом начале находим "Разделы для которых следует игнорировать показ ожидающих изменений в конфигурации" и вписываем туда `bed_mesh default` `bed_mesh adaptive` `prtouch default` должно получится как то так:



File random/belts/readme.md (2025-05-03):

<h3 align="right"><a href="https://www.tinkoff.ru/rm/yakovleva.irina203/51ZSr71845" target="_blank">ваше "спасибо" автору</a></h3>
<h3 align="right"><a href="https://t.me/tombraider2006" target="_blank">телеграм канал автора</a></h3>

<h2>Регулировка натяжения ремней опираясь на графики</h2>

В составе [helper script](https://guilouz.github.io/Creality-Helper-Script-Wiki/helper-script/helper-script-installation/) если вы установили пункт 10  у нас есть  инструмент построения графиков `belts_shaper_calibration` который призван помочь с регулировкой натяжения. Желательно графики ремней рассматривать в совокупности с графиками шейперов.

Внимание! иногда изза переполнения временной папки макрос не может завершить работу и выпадает с ошибкой, в этом случае выключите принтер по питанию и включите снова. если это не помогло то удалите 10 пункт через helper-script, убедитесь что у вас установлен 5 пункт "Gcode shell commands" если нет установите его и поставьте 10 пункт заново.  если вы используете Guppy Screen то ~~да поможет вам бог~~ у вас макрос называется "guppy_belts_calibration" и "guppy_shapers" соответсвенно вместо "test_resonanse_graphs"  

Рассмотрим стандартный график который получают пользователи после первого применения.  

*A1 - левый мотор A2 - правый мотор на графике.*



1 непарные пики,  - если там их  есть - вах, все плохо срочно искать где ремень трется. 

2 до 85% жить можно если художка.  если техничка искать какой ремень перетягивает. если 93-97 расслабиться и жить спокойно, больше 97  - гордится. 

3 и 4 это расхождение между пиками по амплитуде и частоте, в к1 небольшая разница по амплитуде будет всегда, так что не париться, а вот по частоте это когда вправо влево тянет это уже звоночек о неравномерно натянутых ремнях.

Зеленая полоса "Relax_Region", все что в нее попадает не стоит вашего внимания.

Рассмотрим более клиничиские случаи.

<h3>Дополнительный пик</h3>



Однако может быть и вот так:



что является просто сбоем алгоритма, сути не меняет и лечится точно также, поиском ошибок кинематики, трений ремня, задеваний, перекосов.

Также подтверждение мы можем увидеть и на графике шейперов вот 2 графика:



А вот график от этого же принтера только шейперов по игрек:



Низкая амплитуда нам говорит о слабом натяжении ремня, но увидев в графике шейперов размерность 1е4 мы можем предположить что с натяжкой тут все в порядке но есть явное задевание в одном месте.  Такой дефект может быть из-за ослабления  крепления шкива на моторе к примеру.

<h3>Заклинивание осей</h3>

На графике в таком случае мы можем увидеть примерно такое:



или даже так:



 В данном случае можно предположить заклинивание сразу по двум осям,  однако вероятнее всего что из-за перенатяжения одного из ремней, каретка оси стоит наискосок к порталу, что вызывает дергания при тесте второго ремня.  Основанием для такого предположения является слишком большая разница в амплитудах наших графиков. Поэтому разбираться нам надо с осью игрек и смотреть как ходят ремни и правильно ли установлен шкив мотора.  Самый вероятный вариант - перекос зубчатого шкива.

<h3>Расхождения по частоте</h3>

На самом деле найти большие расхождения по частоте в графиках пользователей мне не удалось.  В основном они колеблются в районе 1.5-3 герца. 



или так: 



Это лечится проверкой паралельности портала. как это сделать описано ниже в части расхождение по амплитуде.

<h3>Расхождения по амплитуде</h3>

Несколько примеров:





Самый частый вариант который можем встретить в графиках по ремням.

Для проверки правильного расположения каретки икс можно использовать очень простой способ.  

Выводим нашу голову на середину портала с выключенными моторами.  Подпихивая ее пальцем к переднему краю до упора.





Внимательно смотрим какой край приехал первый и можем проверить нажав с усилием на каждом из концов портала. 



Вероятнее всего что с одной из сторон будет приезжать неодновременно.  Эта разница потом будет влиять на геометрию наших деталей так что задача с помощью регулировки натяжения ремней сократить это расстояние до минимального вплоть до полного отсутсвия зазора. 



Алгоритм исправления. 

    1. Расслабляем оба натяжителя.
    2. Перемещаем печатную голову по кругу, для того чтобы ремни распределили нагрузку и встали ровно. 
    3. затягиваем крепления натяжителя. 
    4. Делаем тест как показано выше. 
    5. если перекос остался при нажатии пальцем вы увидите какой из ремней ослабляется при нажатии. его нам и надо подтянуть.
    6.  расслабляем крепления нужного ремня, натягиваем ремень и затягиваем крепления натяжителя. Повторяем пункты 2 и 4.

Вполне вероятно что график при хорошей регулировке будет выглядеть как то так:



или так:



Небольшая разница по амплитуде в данном случае не страшна и не говорит о плохой регулировке.

Стоит также обратить внимание на размерность. если у вас получилось так: 



Размерность должна быть в пределах 1е5-1е6. 

 *1е7 недотяг* 1е4 недотяг(исправлено по отзывам чата пользователей хотя я думал ровно наоборот). 

<h3>Тестирование</h3>

Правильность наших действий мы можем проверить по [**простой модели**](https://www.thingiverse.com/thing:2563185)



Главное отличие от большинства других калибровочных тестов в том, что углы обрезаны, так что вы можете легко измерить перекос XY вашего принтера. 

После печати мы измеряем модель по сторонам икс и игрек а так же проверяем диагоналям. небольшие(0.01-0.2) отклонения от размеров модели могут быть обусловлены усадкой материала, неточностью в калибровке потока и точности настройки Pressure Advance но значение диагоналей должно быть одинаковым.  

<h5 align="right">поставьте "звездочку" проекту. так другим пользователям легче его найти.</h5>

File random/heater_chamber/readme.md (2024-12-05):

<h3 align="right"><a href="https://www.tinkoff.ru/rm/yakovleva.irina203/51ZSr71845" target="_blank">ваше "спасибо" автору</a></h3>
<h3 align="right"><a href="https://t.me/tombraider2006" target="_blank">телеграм канал автора</a></h3>

<h1>Подключение нагревателя камеры принтера</h1>

При печати высокотемпературными пластиками одним из необходимых параметров для успешной печати является стабильно высокая температура в камере. 

Если вы установили Helper Script пункт **9** **chamber fan** - объедениние температурного датчика камеры принтера и заднего вентилятора.  При превышении пороговой температуры *по умолчанию 35 градусов* задний вентилятор включается высасывая излишне теплый воздух и подкачивая холодный, таким образом стабилизируя температуру печати. Однако этот пункт хорошо работает до температур 45-47 градусов, что далеко не всегда достаточно. Если ваша цель печать на температурах 50-60 градусов то данное руководство для вас.

Не забудьте почитать про 9 пункт Helper Script [тут](/random/menu.md)

<h2>Установка нагревателя</h2>

Нам потребуется несколько проводов, кримпер для обжима разьема, 2pin PH2.0 разьем от него 2 провода:



соблюдайте полярность! сверху на фото +(красный) снизу -(черный)

 пойдут они  до твердотельного реле например [SSR-25DA, Твердотельное реле 220В, коммутация AC 24-380В / 25А, управление DC 3-32В](https://www.ozon.ru/product/ssr-25da-tverdotelnoe-rele-220v-kommutatsiya-ac-24-380v-25a-upravlenie-dc-3-32v-keramicheskiy-korpus-1630953294/)



сперва я хотел использовать простые реле типа таких:



но после того как проработав пару минут умерло 2 штуки я решил что лучше один раз заплатить за нормальное реле. 

я использовал нагреватель с вентилятором такой
с креплением [таким](ptcheater_v1.step) 



Но не могу его рекомендовать так как работает он из рук вон плохо,  однако в сети уже есть несколько проектов которые на вид внушают доверие.  например [этот](https://www.printables.com/model/863675-nexgen3d-chamber-heater)  

Cуть особо не меняется, у нас есть выход на 24 вольта на наш вентилятор и подключаемое реле которое коммутирует цепь 220 вольт. 220 вольт удобно взять на клеммах входа блока питания. 

При установке нагревателя, не забывайте о габаритных размерах стола, проверяйте чтобы оставался зазор как от стола до нагревателя, так и от входа вентилятора до стенки принтера.

**Помните, все работы по подключению проводяться на отключенном питании принтера. Не выключателем! Отключайте кабель физически! Спички детям не игрушки и высокое напряжение тоже. Изолируйте соединения, не трогайте контакты и провода при подключенном принтере.** 



если кто то перерисует схему буду благодарен, художник из меня  так себе.

<h2>Правка конфигурационных файлов</h2>
К сожалению править файл который нам нужен мы не сможем и первым делом нам придется зайти через ssh в наш принтер и вызвав меню helper script 

```
sh /usr/data/helper-script/helper.sh
```
Выбираем пункт `2 remove`

и удаляем 9 пункт `Fans Control Macros`

выходим из консоли.

Не переживайте, часть функционала макроса мы скоро вернем с помощью наших файлов.

далее нам надо в вебпанели найти файл `printer.cfg` и внести в него несколько изменений. 

Находим такой блок и удаляем его:
*или перед строчками ставим знак `#` чтобы закоментировать.*
```
[duplicate_pin_override]
pins: PC0, PC5

[temperature_fan chamber_fan]
pin: PC0
cycle_time: 0.0100
hardware_pwm: false
max_power: 1
shutdown_speed: 0
sensor_type: EPCOS 100K B57560G104F
sensor_pin: PC5
min_temp: 0
max_temp: 70
control: watermark
max_delta: 2
target_temp: 35.0
max_speed: 1.0
min_speed: 0.0
```

После строки `[include Helper-Script/KAMP/KAMP_Settings.cfg]`

вписываем:

```
[include fan_control.cfg]
```

сохраняем файл без перезагрузки. 

скачиваем файл [fan_control.cfg](/random/heater_chamber/fan_control.cfg) 

или если у вас проблемы со скачиванием то 
создаем новый файл в корневой папке конфига(рядом с `printer.cfg`) и называем его `fan_control.cfg`

открываем его для редактирования и копируем туда следующий блок:

```
########################################
# Fans Control
########################################

[respond]

[duplicate_pin_override]
pins: PC5, PB2, PC6, ADC_TEMPERATURE

[temperature_fan soc_fan]
pin: PB2
cycle_time: 0.0100
kick_start_time: 0.5
hardware_pwm: false
max_power: 1
shutdown_speed: 0
sensor_type: temperature_mcu
min_temp: 0
max_temp: 100
control: watermark
max_delta: 2
target_temp: 45.0
max_speed: 1.0
min_speed: 0.0
tachometer_pin:PC6

[heater_generic chamber]
heater_pin:PA0
max_power:1.0
sensor_type: EPCOS 100K B57560G104F
sensor_pin: PC5
control: watermark
max_delta: 1
min_temp:-100
max_temp:65

[verify_heater chamber]
max_error: 900
check_gain_time: 300
hysteresis: 50
heating_gain: 1

[gcode_macro M141]
gcode:
    {% if printer["heater_generic chamber"] is defined %}
         {% set s = params.S|float %}
        SET_HEATER_TEMPERATURE HEATER=chamber TARGET={params.S|default(0)}
    {% endif %}

[gcode_macro M191]
description: Wait for Chamber Temperature to heat up
gcode:
  {% set s = params.S|float %}
  {% set chamber_temp = printer["heater_generic chamber"].temperature|float %}
  {% if s > 0 %}
    M141 S{s}
  {% endif %}
  {% if s > chamber_temp and s <= 65 %}
    M140 S100
    M106 P2 S210 # подключение боковой улитки для лучшей конвекции в камере
    RESPOND TYPE=command MSG="Waiting for the bed to heat up the chamber..."
    TEMPERATURE_WAIT SENSOR="heater_generic chamber" MINIMUM={s-2}
    RESPOND TYPE=command MSG="Chamber target temperature reached: {s}°C"
    M107 P2 S0 # отключение улитки при достижении нужной температуры
    M140 S{s}
  {% endif %}

[gcode_macro M106]
gcode:
  {% set fans = printer["gcode_macro PRINTER_PARAM"].fans|int %}
  {% set fan = 0 %}
  {% set value = 0 %}
  {% if params.P is defined %}
    {% set tmp = params.P|int %}
    {% if tmp < fans %}
      {% set fan = tmp %}
    {% endif %}
  {% endif %}
  {% if params.S is defined %}
    {% set tmp = params.S|float %}
  {% else %}
    {% set tmp = 255 %}
  {% endif %}
  {% if tmp > 0 %}
    {% if fan == 0 %}
      {% set value = (255 - printer["gcode_macro PRINTER_PARAM"].fan0_min) / 255 * tmp %}
      {% if printer['gcode_macro Qmode'].flag | int == 1 %}
        SET_GCODE_VARIABLE MACRO=Qmode VARIABLE=fan0_value VALUE={printer["gcode_macro PRINTER_PARAM"].fan0_min + value}
        {% if value > (255 - printer['gcode_macro PRINTER_PARAM'].fan0_min) / 2  %}
          {% set value = printer["gcode_macro PRINTER_PARAM"].fan0_min + (255 - printer['gcode_macro PRINTER_PARAM'].fan0_min) / 2 %}
        {% else %}
          {% set value = printer["gcode_macro PRINTER_PARAM"].fan0_min + value %}
        {% endif %}
      {% else %}
        {% set value = printer["gcode_macro PRINTER_PARAM"].fan0_min + value %}
      {% endif %}
    {% endif %}
    {% if fan == 1 %}
      {% set value = (255 - printer["gcode_macro PRINTER_PARAM"].fan1_min) / 255 * tmp %}
      {% if printer['gcode_macro Qmode'].flag | int == 1 %}
        SET_GCODE_VARIABLE MACRO=Qmode VARIABLE=fan1_value VALUE={printer["gcode_macro PRINTER_PARAM"].fan1_min + value}
        {% if value > (255 - printer['gcode_macro PRINTER_PARAM'].fan1_min) / 2  %}
          {% set value = printer["gcode_macro PRINTER_PARAM"].fan1_min + (255 - printer['gcode_macro PRINTER_PARAM'].fan1_min) / 2 %}
        {% else %}
          {% set value = printer["gcode_macro PRINTER_PARAM"].fan1_min + value %}
        {% endif %}
      {% else %}
        {% set value = printer["gcode_macro PRINTER_PARAM"].fan1_min + value %}
      {% endif %}
    {% endif %}
    {% if fan == 2 %}
      {% set value = (255 - printer["gcode_macro PRINTER_PARAM"].fan2_min) / 255 * tmp %}
      {% if printer['gcode_macro Qmode'].flag | int == 1 %}
        SET_GCODE_VARIABLE MACRO=Qmode VARIABLE=fan2_value VALUE={printer["gcode_macro PRINTER_PARAM"].fan2_min + value}
        {% if value > (255 - printer['gcode_macro PRINTER_PARAM'].fan2_min) / 2  %}
          {% set value = printer["gcode_macro PRINTER_PARAM"].fan2_min + (255 - printer['gcode_macro PRINTER_PARAM'].fan2_min) / 2 %}
        {% else %}
          {% set value = printer["gcode_macro PRINTER_PARAM"].fan2_min + value %}
        {% endif %}
      {% else %}
        {% set value = printer["gcode_macro PRINTER_PARAM"].fan2_min + value %}
      {% endif %}
    {% endif %}
  {% endif %}
  {% if value >= 255 %}
    {% set value = 255 %}
  {% endif %}
  {% if params.P is defined and params.P|int == 3 %}
    {% set fan = 1 %}
  {% endif %}
  SET_PIN PIN=fan{fan} VALUE={value}
```

сохраняем, закрываем. Переходим к файлу `gcode_macro.cfg`

ищем макрос который начинается с **[gcode_macro M106]** удаляем либо закомментируем все строки в этом блоке.
также поступаем с макросом **[gcode_macro M141]**. сохраняем и теперь уже с перезагрузкой. если все правильно то ваша панель температур будет выглядеть как то так:

 

на данный момент задний вентилятор теперь просто вентилятор, но вы всегда можете предложить как его использовать в [нашем чате телеграмм тут](https://t.me/crealityK1rus). 

<h2>Небольшое послесловие</h2>

В данном руководстве температура нагрева ограничена 65 градусами. Никто вам не сможет помешать поставить и больше, но помните. уже после 63 градусов нагрева камеры у пользователей начинаются проблемы: 
  
 * Из-за недостаточного обдува вентилятора радиатора возможны пробки. 
  
 * Двигатели всех осей работают при повышенных температурах на которые не расчитывал производитель.

 * Из-за нагрева дна принтера это тепло передается на материнскую плату и блок питания,  советую распечатать [крепление вентилятора материнской платы](https://www.printables.com/model/540070-motherboard-fan-mount-mk2-collection-creality-k1-s) или [такое](https://www.printables.com/model/540070-motherboard-fan-mount-mk2-collection-creality-k1-s)  и удалить металлическую крышку дна принтера для обеспечения лучшего охлаждения.

  * В материнской плате которая управляет мотором фидера и установлена в печатной голове принтера возможны сбои изза перегрева.

 * Учитывайте что обдув ваших моделей будет происходить внутри замкнутого пространства и той же повышенной температурой. Увеличивайте процент обдува нависаний.

  В составе кода есть два макроса контроля температуры:
  
  **M141** как использовать контроль температуры в слайсере описание тут - 9 пункт Helper Script [тут](/random/menu.md) 

  **M191** В отличии от обычного макроса который включает нагрев стола, мы включаем и стол и нагреватель и вентилятор боковой улитки для лучшей конвекции воздуха. Не начинаем печать до того как не набрали целевую температуру.

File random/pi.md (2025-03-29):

<h2>Зачем нам одноплатник</h2>

Если у вас нет еще умного дома и есть принтер то хорошей покупкой может стать небольшой одноплатный компьютер расширяющий возможности нашего принтера.

Дело в том что на принтере устанавлена сильно кастрированная операционная система, которая не даст воспользоваться благами цивилизации которые возможны с обычным клиппером. Рассматривать примеры мы будем на примере Orange PI мою статью по установке операционной системы на нее можно почитать [тут](https://3d-diy.ru/blog/ustanovka-os-na-orange-pi-3-lts/)

<h3>Telegram Bot</h3>

Уведомления в боте контроль  параметров во время печати, все это и многое другое доступно при использовании телеграм бота. вот пример что можно увидеть при использовании:



чтобы это заработало на удаленном сервере необходимо поставить [KIAUH](https://github.com/dw-0/kiauh) создать папку `/home/pi/printer_data/config`  и в ней положить конфиг телеграмм бота `telegram.conf`

содержимое файла:

```
[bot]
server: ваш_IP:7125
bot_token: ваш токен
chat_id: ваш чат айди

[camera]
host: http://ваш_IP:4408//webcam/?action=stream

[progress_notification]
time: 60

[telegram_ui]
buttons: [status,pause,cancel,resume],[files,emergency,macros,shutdown]
silent_progress: true
hidden_macros: ACCURATE_G28, AUTOTUNE_SHAPERS, BED_LEVELING, BED_MESH_CALIBRATE, END_PRINT_POINT, DEFINE_OBJECT, END_CURRENT_OBJECT, END_PRINT, END_PRINT_POINT_WITHOUT_LIFTING, FIRST_FLOOR_PAUSE, FIRST_FLOOR_PAUSE_POSITION, FIRST_FLOOR_RESUME, G29, GET_TIMELAPSE_SETUP, HYPERLAPSE, INPUTSHAPER, KAMP_BED_MESH_SETTINGS, KAMP_PURGE_LINE_SETTINGS, KLIPPER_BACKUP_CONFIG, KLIPPER_RESTORE_CONFIG, LIST_EXCLUDED_OBJECTS, LIST_OBJECTS, LOAD_MATERIAL, LOAD_MATERIAL_CLOSE_FAN2, LOAD_MATERIAL_RESTORE_FAN2, M106, M107, M141, M191, M204, M205, M900, MOONRAKER_BACKUP_DATABASE, MOONRAKER_RESTORE_DATABASE, PID_BED, PRINT_CALIBRATION, PRINT_PREPARE_CLEAR, PRINT_PREPARED, PRINTER_PARAM, QUIT_MATERIAL, REMOVE_ALL_EXCLUDED, RESTORE_E_CURRENT, SET_E_MIN_CURRENT, SET_GCODE_OFFSET, START_CURRENT_OBJECT, START_PRINT, TEST_STREAM_DELAY, TIMELAPSE_RENDER, TUNOFFINPUTSHAPER, TIMELAPSE_TAKE_FRAME, WAIT_TEMP_END, WAIT_TEMP_START, XYZ_READY

silent_commands: true

[status_message_content]
content: progress, height, filament_length, filament_weight, print_duration, eta, finish_time, m117_status, tgnotify_status, last_update_time
sensors: mcu, chamber_temp
heaters: extruder, heater_bed, orange_pi, mcu_temp
fans: fan0, chamber_fan, soc_fan, fan2

```
не забываем поправить ip принтера а также вставить чат айди и токен.  больше инструкций можно найти на [вики проекта](https://github.com/nlef/moonraker-telegram-bot)

<h3>Spoolman</h3>

Spoolman — это самостоятельный веб-сервис, разработанный для того, чтобы помочь вам эффективно управлять катушками филамента для 3D-принтера и контролировать их использование. Он действует как централизованная база данных, которая легко интегрируется с популярным программным обеспечением для 3D-печати, Klipper / Moonraker . При подключении он автоматически обновляет вес катушек по мере печати, предоставляя вам информацию об использовании филамента в режиме реального времени.

Функции:
+ Управление нитью : ведите подробный учет типов филамента, производителей и отдельных катушек.
+ Интеграция API : API REST обеспечивает простую интеграцию с другим программным обеспечением, облегчая автоматизацию рабочих процессов и обмен данными.
+ Обновления в режиме реального времени : будьте в курсе событий благодаря обновлениям в режиме реального времени через Websockets, обеспечивая немедленную обратную связь во время операций печати.
+ Центральная база данных филаментов : поддерживаемая сообществом база данных производителей и нитей упрощает добавление новых катушек в ваш инвентарь. 
+ Веб-клиент : Spoolman включает в себя встроенный веб-клиент, который позволяет вам легко управлять данными:
Просмотр, создание, редактирование и удаление данных о филаментах.
+ Добавьте пользовательские поля, чтобы адаптировать информацию к вашим конкретным потребностям.
+ Печатайте этикетки с QR-кодами для легкой идентификации и отслеживания катушек.

+ Управление несколькими принтерами : позволяет одновременно обрабатывать обновления спула с нескольких принтеров.



после установки [отсюда](https://github.com/Donkie/Spoolman)

необходимо указать в файле `moonraker.conf` следующие строки

```
[spoolman]
server: http://ваш_IP:7912
#   URL to the Spoolman instance. This parameter must be provided.
sync_rate: 5

```
вместо `ваш_IP` указываем ip-адрес сервера spoolman



почитать про интеграцию spoolman в orcaslicer [**можно тут**](https://t.me/tombraider2006/92)

<h3>KlipperScreen</h3>

Если у вас есть экран с тач скрином ну или лишний монитор с мышкой то ваш одноплатник может выступить в качестве дополнительного экрана вашего принтера, даже если он находится в другой комнате)



Необходимо поставить [KIAUH](https://github.com/dw-0/kiauh) и через него установить klippersreen более подробно можно почитать [тут](https://github.com/KlipperScreen/KlipperScreen)

содержимое файла KlipperScreen.conf в папке `/home/pi/printer_data/config`

```
[printer k1]
# Camera configuration
#camera_url: http://ваш_IP:4408//webcam/?action=stream
# Define the moonraker host/port if different from 127.0.0.1 and 7125
moonraker_host: ваш_IP
moonraker_port: 7125

```
`ваш_IP` замениете на адрес вашего принтера в локальной сети. 



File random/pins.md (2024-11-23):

<h2>Добавление функционала на основе virtual_pins на примере отключения вентиляторов в конце печати.</h2>

Тут попросили меня реализовать не очень полезную идею по отключению вентиляторов в конце печати, ну так то идея так себе, но *раз звезды зажигают - значит это кому то нужно.* 

Итак идея. необходимо дать команду в слайсере для определенного пластика чтобы при окончании печати он не включал обдув а просто заканчивал печать. 

сам макрос END_PRINT выглядит так:

```
[gcode_macro END_PRINT]
gcode:
  Qmode_exit
  EXCLUDE_OBJECT_RESET
  PRINT_PREPARE_CLEAR
  M220 S100
  SET_VELOCITY_LIMIT ACCEL=5000 ACCEL_TO_DECEL=2500
  TURN_OFF_HEATERS
  M107 P1
  M107 P2
  END_PRINT_POINT
  WAIT_TEMP_START
  M84
```
часть отвечающая за старт работы кулеров это `WAIT_TEMP_START` Необходимо обрамить ее условиями и для этого применим модуль virtual_pins (если у вас по каким то причинам нет этого модуля это легко исправить - достаточно в /klippy/extras/ добавить [virtuals_pins.py](virtual_pins.py) и добавить в `printer.cfg` раздел  `[virtual_pins]` )

Начнем с того что в printer.cfg добавим саму кнопку. Важно! код необходимо вставить после раздела `[virtual_pins]`

```
[output_pin FAN_END_STOP]
pin: virtual_pin:FAN_END_STOP_pin
value: 0
```

фантазии у меня нет, так что название выдумал такое, какое пришло в голову.

сохраняем перегружаем смотрим. Должно получится как то так:



по умолчанию он у нас будет выключен. 

теперь идем в gcode_macro.cfg находим END_PRINT и обрамляем макрос WAIT_START условиями

```
[gcode_macro END_PRINT]
gcode:
  Qmode_exit
  EXCLUDE_OBJECT_RESET
  PRINT_PREPARE_CLEAR
  M220 S100
  SET_VELOCITY_LIMIT ACCEL=5000 ACCEL_TO_DECEL=2500
  TURN_OFF_HEATERS
  M107 P1
  M107 P2
  END_PRINT_POINT
  {% if printer['output_pin FAN_END_STOP'].value == 0 %}
    WAIT_TEMP_START
  {% else %}
    SET_PIN PIN=FAN_END_STOP VALUE=0
  {% endif %}
  M84
```

По умолчанию мы назначили значение нашей кнопки 0 и проверив условия когда у нас значение равно 0 принтер продолжит выполнение макроса и выполнит  WAIT_START но если мы переведем нашу кнопку в значение 1 мы эту строку перепрыгнем. Чтобы после печати кнопка наша вернулась в исходное состояние в конце дописываем значения кнопки 0.

Теперь если мы включим нашу виртуальную кнопку в конце печати кулер головы не будет дуть на наш хотенд.  но хотелось бы это внести в слайсер. Да легко! В орке открываем профиль нужного пластика и лезем на вкладку дополнительно и вписываем переключение нашей кнопки. кстати синтаксис ее нажатия можно всегда подсмотреть в консоли клиппера.

вписываем 

```
SET_PIN PIN=FAN_END_STOP VALUE=1
```

получится как то так:



всё. готово.

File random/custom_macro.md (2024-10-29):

<h3 align="right"><a href="https://www.tinkoff.ru/rm/yakovleva.irina203/51ZSr71845" target="_blank">ваше "спасибо" автору</a></h3>
<h3 align="right"><a href="https://t.me/tombraider2006" target="_blank">телеграм канал автора</a></h3>
<h5 align="right">поставьте "звездочку" проекту. так другим пользователям легче его найти.</h5>

Про файлик /usr/share/klipper/klippy/extras/custom_macro.py

в этом файле собрана почти вся дичь которую внесли китайские разработчики. Для тех кто пользовался клиппером до этого, будет легче понять отличия от стандартного клиппера.

Этот макрос является классом с именем "CUSTOM_MACRO". Внутри него есть различные функции и переменные для управления печатью и калибровкой.

В функции `init` происходит инициализация объектов и переменных макроса. Внутри данной функции мы можем видеть следующие строки кода:
- `self.printer = config.get_printer()`: Получение объекта printer.
- `self.gcode = self.printer.lookup_object('gcode')`: Получение объекта gcode.
- `self.pheaters = None`: Инициализация переменной pheaters как None.
- `self.heater_hot = None`: Инициализация переменной heater_hot как None.
- `self.extruder_temp=None`: Инициализация переменной extruder_temp как None.
- `self.bed_temp=None`: Инициализация переменной bed_temp как None.
- `self.prtouch = None`: Инициализация переменной prtouch как None.

Далее в макросе происходит регистрация различных команд для G-кода, таких как:
- `CX_PRINT_LEVELING_CALIBRATION`: Команда для запуска процесса калибровки.
- `CX_CLEAN_CALIBRATION_FLAGS`: Команда для очистки флагов калибровки.
- `CX_PRINT_DRAW_ONE_LINE`: Команда для рисования одной линии печати.
- `CX_ROUGH_G28`: Команда для выполнения шага G28 (возврат осей в исходное положение).
- `CX_NOZZLE_CLEAR`: Команда для очистки сопла.

Затем в макросе есть несколько переменных, таких как:
- `self.default_extruder_temp`: Значение температуры экструдера по умолчанию.
- `self.default_bed_temp`: Значение температуры стола по умолчанию.
- `self.g28_ext_temp`: Температура экструдера для выполнения шага G28.
- `self.nozzle_clear`: Флаг для указания, нужно ли выполнять очистку сопла.
- `self.calibration`: Значение параметра calibration.

Далее следуют функции для команд, такие как `cmd_CX_PRINT_LEVELING_CALIBRATION`, `cmd_CX_CLEAN_CALIBRATION_FLAGS` и другие. В каждой функции происходит выполнение определенной операции по заданной команде.

Например, в функции `cmd_CX_PRINT_LEVELING_CALIBRATION` выполняется скрипт `'CHECK_BED_MESH AUTO_G29=1'`, который запускает процесс проверки сетки стола и автоматической калибровки.

В функции `cmd_CX_CLEAN_CALIBRATION_FLAGS` происходит просто установка переменной `self.leveling_calibration` в значение 0.

макрос представляет класс "CUSTOMMACRO", который содержит несколько методов и переменных для управления печатью.

В методе "init" инициализируются различные переменные, такие как "printer" (доступ к объекту принтера), "gcode" (доступ к объекту G-кода), "pheaters" (нагреватели), "heaterhot" (нагреватель для экструдера), "extrudertemp" (температура экструдера), "bedtemp" (температура стола), "prtouch" (объект PRTouch для автоматической калибровки), а также регистрируются различные команды G-кода.

Метод "getstatus" возвращает текущий статус некоторых переменных.

Метод "cmdCXPRINTLEVELINGCALIBRATION" выполняет команду G-кода "CHECKBEDMESH AUTOG29=1" для автоматической калибровки стола.

Метод "cmdCXCLEANCALIBRATIONFLAGS" устанавливает переменную "levelingcalibration" в 0 для очистки флагов калибровки.

Метод "cmdCXROUGHG28" выполняет грубую калибровку путем установки температур экструдера и стола, запуска G-кода G28 для перемещения осей в начальное положение и выполняет другие команды G-кода, такие как изменение минимальной температуры для PRTouch и запуск M104 и M140 для установки заданных температур экструдера и стола.

Метод "cmdCXNOZZLECLEAR" запускает команду G-кода "NOZZLECLEAR" с заданными пределами температур для очистки сопла.

Функция "loadconfig" загружает и возвращает объект класса "CUSTOMMACRO" с конфигурацией.

Метод cmd_CX_PRINT_LEVELING_CALIBRATION запускает функцию печати и принимает три параметра: EXTRUDER_TEMP (от 180 до 300), BED_TEMP (от 0 до 100) и CALIBRATION (0 или 1). Этот метод выполняет скрипт 'CHECKBEDMESH AUTOG29 = 1' для калибровки стола.

Метод `cmdCXCLEANCALIBRATIONFLAGS` очищает флаги калибровки, устанавливая `levelingcalibration в 0.

Метод cmdCXROUGHG28` выполняет "грубую" калибровку стола и работает следующим образом:
- Устанавливает температуру экструдера (`extrudertemp) в значение параметра EXTRUDERTEMP`. Если параметр не указан, используется значение по умолчанию, заданное в конфигурации (`defaultextrudertemp`). Значение должно быть в диапазоне от 180.0 до 320.0.
- Вычисляет температуру экструдера для команды G28 (`g28exttemp`) путем вычитания 70 из значения `extrudertemp. Если результат превышает 180.0, g28exttemp устанавливается равным 180.0.
- Ищет объект prtouchv2` или `prtouch` и присваивает его переменной `prtouch`. Если объект не найден, выводится информация, что `prtouch = prtouch`.
- Устанавливает температуру стола (`bedtemp) в значение параметра BEDTEMP`. Если параметр не указан, используется значение по умолчанию, заданное в конфигурации (`defaultbedtemp`). Значение должно быть в диапазоне от 0.0 до 130.0.
- Устанавливает значение `levelingcalibration в значение параметра LEVELINGCALIBRATION`. Если параметр не указан, используется значение по умолчанию, которое равно 1.
- Запускает скрипты G-кода для установки температуры экструдера и стола: 'M104 S%d' и 'M140 S%d', соответственно.
- Вызывает скрипт G28 для грубой калибровки стола.
- (Закомментированная строка `NOZZLECLEAR предположительно используется для очистки сопла, но в данном случае не выполняется.)

Метод cmdCXNOZZLECLEAR` выполняет очистку сопла с заданными температурами, используя команду G-кода 'NOZZLECLEAR HOTMINTEMP = %d HOTMAXTEMP = %d BEDMAXTEMP = %d'. Значения температур берутся из g28_ext_temp, extruder_temp и bed_temp, соответственно.

Метод cmd_CX_PRINT_DRAW_ONE_LINE выполняет рисование одной линии перед печатью и работает следующим образом:
- Запускает скрипты G-кода для установки относительных координат ('M83') и перемещает печатающую головку в начальную точку ('G1 X10 Y10 Z2 F6000').
- Запускает скрипты G-кода для опускания печатающей головки ('G1 Z0.1 F600').
- Ищет объекты pheaters, heater_hot и extruder и сохраняет соответствующие ссылки.
- Выводит информацию о флаге can_break_flag через gcode.respond_info.
- Устанавливает температуру экструдера (extruder_temp) через M104 и температуру стола (bed_temp) через M140.
- Устанавливает температуру экструдера через pheaters.set_temperature и ожидает, пока флаг can_break_flag не станет равным 1. Флаг can_break_flag определяется вызовом pheaters.can_break_flag.
- Если can_break_flag равен 3, меняет флаг на 0 и выполняет ряд команд G-кода, включая установку ограничений скорости, температур и перемещения печатающей головки.

спасибо пользователю https://t.me/Ale_xe_y_0 за предоставленный материал

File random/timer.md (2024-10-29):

<h3 align="right"><a href="https://www.tinkoff.ru/rm/yakovleva.irina203/51ZSr71845" target="_blank">ваше "спасибо" автору</a></h3>
<h3 align="right"><a href="https://t.me/tombraider2006" target="_blank">телеграм канал автора</a></h3>

<h1>таймер отложенной печати</h1>

предположим время вечер, просыпаться поутру лень, некогда, или, например, хочу чтоб принтер начал печатать в три ночи чтоб к утру  заменить филамент и к обеду распечатать, так вот, нет у него такой функции чтоб по будильнику печатать. можно конечно через HOME ASSITANT и прочие умные домики, но это вроде как не спортивно...

**Внимание! так как в новых версиях Хелпер скрипта уже этот модуль есть то пункт 1 пропускаем**

итак приступаем:
 
 **1.** заходим по ssh на принтер и вписываем (если ставили хелпер скрипт и пункт 6 в нем то это можно пропустить, я уже инициировал добавку виртуал пинов в хелпер скрипте)

```
cd /usr/share/klipper/klippy/extras
wget --no-check-certificate https://raw.githubusercontent.com/Tombraider2006/K1/main/random/virtual_pins.py

```

 **2.** далее открываем  `printer.cfg`  например через вебпанель и вписываем в любое свободное место: 

```
[virtual_pins] # если хелпер скрипт установлен то эту строку стоит закоментировать
[output_pin timer]
pin: virtual_pin:timer_pin
pwm: True
value: 0
scale: 1440

[delayed_gcode wait_timer] 
 # initial_duration: 2.
gcode:
    {% if printer['output_pin timer'].value > 0 %}
    {% set WAIT = printer['output_pin timer'].value * 1440|float %}
    {% set WAIT_ROUNDED = WAIT|int %}
    {% if WAIT - WAIT_ROUNDED >= 0.5 %}
    {% set WAIT_ROUNDED = WAIT_ROUNDED + 1 %}
    {% endif %}
      RESPOND MSG="Waiting... {WAIT_ROUNDED} minutes remaining."
      {% set WAIT_ROUND_COUNT = WAIT_ROUNDED - 1 %}
      SET_PIN PIN=timer VALUE={WAIT_ROUND_COUNT}
      UPDATE_DELAYED_GCODE ID=wait_timer DURATION=60
      WAIT_TIMER_START
    {% else %}
     RESPOND MSG="Wait Time End"
     WAIT_TIMER_END	
    {% endif %}

[gcode_macro WAIT_TIMER_START]
gcode:
  UPDATE_DELAYED_GCODE ID=wait_timer DURATION=1
  {% for s in range(0, 4) %}
  SET_PIN PIN=LED VALUE=0.25
  G4 P14000
  SET_PIN PIN=LED VALUE=0.5
  G4 P1000
  {% endfor %}

[gcode_macro WAIT_TIMER_END]
gcode:
  UPDATE_DELAYED_GCODE ID=wait_timer DURATION=0
  SET_PIN PIN=LED VALUE=1

```
сохраняем без перезагрузки

**3.**  в папке /Helper-Script/KAMP ищем файл `Start_Print.cfg`
   и сразу после строки `gcode:` нажимаем Enter и вписываем:
```
WAIT_TIMER_START
```

получится как то так как то так:



сохраняем, перегружаемся. 

4. теперь в интерфейсе появился новый элемент:



Теперь если перед печатью ввести в окошко значения количество минут (вплоть до 1440 что равно 24 часам) то печать стартует только после этого времени.  все это время принтер будет иногда вам помаргивать светом подсветки раз в 14 секунд.  
если вы передвинете ползунок на новое значение в течении минуты обновится значение таймера, если скинуть на ноль то печать начнется как только пройдет минута или меньше. 

если при запуске появилась вот такая ошибка


в файле `printer.cfg` добавьте в любом месте раздел 
```
[respond]
```

P.P.S если вы не можете отредактировать файл /Helper-Script/KAMP/Start_Print.cfg это от того что это у вас не папка а ссылка на папку.   вы можете отредактировать /usr/data/KAMP-for-K1-Series/Configuration/Start_Print.cfg или всю папку переписать в /usr/data/printer_data/config/Helper-Script/KAMP удалив ссылку на папку. 

[**thank a lot for assistance in writing the macro -  Guilouz**](https://github.com/Guilouz)

<h5 align="right">поставьте "звездочку" проекту. так другим пользователям легче его найти.</h5>

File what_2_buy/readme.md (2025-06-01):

<h5 align="right">поставьте "звездочку" проекту. так другим пользователям легче его найти.</h5>

Что купить.

Перед каждым владельцем принтера встает вопрос что купить для исправления известных косяков китайского чуда техники, что нужно для лучшей печати и что необязательно. Универсального ответа не существует, так как финансовые возможности у всех разные и цели покупки тоже. Рассмотрим несколько вариантов для возможного апгрейда. Также я постараюсь пояснить что и для чего.

<h1>Must have</h1> обязательный набор

1. **сопла**. расходник всегда нужный в хозяйстве. как узнать какое сопло у вас смотрим тут. заказывать можно везде. избегаем с золотым названием к1с на картинке модели(выпадает металлическая вставка сопла.)

2. [**Пеи пластина.**](https://aliexpress.ru/item/1005008055608486.html) родная пластина у всех моделей к серии страдает тонкостью металла самой пластины. Из-за этого излишняя бугристость. также слишком мягкое покрытие самой пластины, поэтому на ней появляются  точки от сопла во время проведения тестов которые потом могут быть видны на модели. Наш земляк из челябинска производит альтернативое адгезивное покрытие на популярные модели принтеров по уникальной методе.  Это сендвич из 0.5мм пружинной стали и 0.5 FR4. Главная особенность fr4 - можно печатать таким отличным инженерным пластиком как наполненный полипропилен БЕЗ клея. Для остальных пластиков советую использовать адгезив. + возможно печатать как на стороне с текстолитом, так и на металле. при стоимости +- как поделие китайцев вы получаете очень долговременное прочное качественное покрытие для вашего стола. [**купить можно тут**](https://www.avito.ru/chelyabinsk/orgtehnika_i_rashodniki/pokrytiya_dlya_3d_printerov_fr4_na_stalnoy_podlozhke_4084946323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) (за рекламу денег не просил и не давали. классная штука реально)

3. **hotend в сборе.** этот пункт посвящается всем новичкам которые лезут в принтер.   керамический нагреватель штука нежная, процесс откручивания сопла пассатижами и прочие извращения приведут вас к однозначному результату. покупаем, запоминаем что сначала надо читать потом делать. не повторяем ошибок. 

4. **смазка** винты по Z оси валы за ней и валы оси Y(справа и слева портала) смазываем консистентной смазкой атеко или "вмп авто синия"(поиск в любом маркетплейсе). Валы по X(на которой голова) мажем "масло для швейных машин". переодичность смазки: 20-40 часов работы маслом, 50-70 консинтентной. 

<h1>Advanced</h1> продвинутый набор.

1. [**шкивы на 20 зубов 2 штуки внутренний диаметр 5мм**](https://aliexpress.ru/item/33025995477.html) в моделях к1\к1max. В максах не так критично, за счет более длинного тракта ремней. в к1 настоятельно необходима для снижения ряби на деталях. *неактуально в новых ревизиях с 06.24 для к1макс с 02.25 для всех моделей выпущенных после этой даты*
  
2. **SFS** замена стандартного датчика на датчик с детектером движения. подробное описание читаем [тут](https://github.com/Tombraider2006/K1/tree/main/sfs)

3. [**Новая ревизия хотенда с улучшенным радиатором**](https://creality-3d.ru/goods/Komplekt-nagrevatelnogo-bloka-keramicheskij-Sreality-dlya-3D-printera-K1-Max-5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) Призвана уменьшить число отказов при печати легкоплавкими пластиками изза перегрева холодной части радиатора и размягчения пластика в нём.

*к смарт филамент сенсору, надо приложить руки.
Его надо разобрать и смазать ось , иначе её съест быстро*

<h1>Ultimate</h1> максимально приближаемся к идеалу (ха-ха)

1. **замена моторов в моделях к1** вместе со шкивами например на [**такие**](https://aliexpress.ru/item/1005004731197516.html) позволяет чуть снизить шум(не доказано) и чуть снизить рябь относительно родных моторов(процентов на 5-10 меньше)

2. **пластина и грелка стола для К1\К1С**. сам [стол](https://aliexpress.ru/item/1005006877889446.html) [грелка](https://aliexpress.ru/item/1005006917286709.html) к нему. 

В рекомендации попал исключительно как замена если с родным столом чтото случилось, а денег у вас много. 

3. **замена хотенда** для к1\к1макс первых ревизий тут [**купить тут**](https://aliexpress.ru/item/1005005888020698.html) для остальных ревизий и к1с [**купить тут**](https://aliexpress.ru/item/1005007051362908.html) ИЛИ ->
4.  [**Новая ревизия хотенда с улучшенным радиатором**](https://creality-3d.ru/goods/Komplekt-nagrevatelnogo-bloka-keramicheskij-Sreality-dlya-3D-printera-K1-Max-5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) Призвана уменьшить число отказов при печати легкоплавкими пластиками изза перегрева холодной части радиатора и размягчения пластика в нём.
5.  [**Фидер от Фаетус**](https://aliexpress.ru/item/1005009096714497.html). по заверениям производителя призван улучшить печать ТПУ филаментов, уменьшить процент пробок за счет лучшего отвода тепла, улучшенный зацеп филамента также наличие датчика филамента непосредственно в фидере. размещается на штатные места не требует изменения конфига. 

<h2>Магазин запчастей</h2>

Бывает так, что сломалось что то неожиданно и в самый ненужный момент и ждать запчасть из китая останавливая на это время принтер совсем не вариант. Выбирать из наших маркет плейов между теми же китайцами и сомнительными вариантами тоже не хочется. Теперь выход есть. магазин запчастей Creality на площадке OZON от знаменитого в узких кругах **Геннадия 3Д**  [**магазин на озон**](https://ozon.ru/t/14yw68B) или тут [**магазин в россии**](https://creality-3d.ru/catalog/K1C) Здесь вы можете быть уверены что покупаете действительно запчасти от Creality которые дойдут до вас в самый короткий срок.  Да ценник отличается от алиэкспресс но когда вам необходимо починить принтер "вчера", это оправдано.

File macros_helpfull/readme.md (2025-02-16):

<h3 align="right"><a href="https://www.tinkoff.ru/rm/yakovleva.irina203/51ZSr71845" target="_blank">ваше "спасибо" автору</a></h3>
<h3 align="right"><a href="https://t.me/tombraider2006" target="_blank">телеграм канал автора</a></h3>
<h5 align="right">поставьте "звездочку" проекту. так другим пользователям легче его найти.</h5>

**список полезных макросов с пояснениями**

После установки хелпер скрипта открывая вашу панель вы можете увидеть огромную "простыню" с всевозможными макросами. В основном они системные и не предполагают никакого взаимодействия с вами. Они от системы для системы и про систему. Чтобы не путаться и не захламлять интерфейс можно провести несколько простых операций:

1 - открываем настройки

2 - нажимаем макросы

3 - добавить категорию

4 - вписываем название категории (у меня это "тесты")

5 - жмем сохранить



Теперь переходим в раздел "вне категории" и по следующему списку выбираем макрос и нажимаем на него и выбираем ему нашу свежесозданную категорию



`BELTS_SHAPER_CALIBRATION` делает тест резонансов и создает график натяжения ремней

`EXCITATE_AXIS_AT_FREQ` макрос тестирования на определенной частоте резонансов для выявления дефектов сборки



На картинке выше мы видим значения по умолчанию. на частоте 25 герц в течении 10 секунд трясем осью икс.  для проведения теста мы ставим 3-5 секунд и перебором частот 25, 27, 30.. и т.д. находим частоту на которой вибрации максимальны. Далее ставим время теста 30-40 секунд и пальпируя корпус находим узел который  вызывает резонанс.  Внешним осмотром выявляем проблему(выкрутился болтик, отклеилась панель, недотянут винт и прочее)  

`INPUT_SHAPER_CALIBRATION` делает тест резонансов и записывает результат в `printer.cfg`

`MOONRAKER_BACKUP_DATABASE` макрос для создания базы данных со статистикой печати (сколько всего потрачено материала, общего времени и прочего). Необходим для сохранения статистики перед обновлением если вам душу греют эти цифры и вы хотите продолжить считать количество времени и пластика потраченного вашим принтером.

`PID_HOTEND` это процедура калибровки, которая гарантирует, что принтер всегда будет поддерживать стабильную заданную температуру . PID (пропорционально-интегральная производная) используется в принтерах для поддержания стабильной температуры в хотенде.

`RELOAD_CAMERA` в принтерах креалити есть проблема с вебкамерами. иногда, при высоких температурах в камере принтера, они могут выключаться от перегрева. Данный макрос поможет перегрузить сервисы камеры без перезагрузки по питанию.

`TEST_RESONANCES_GRAPHS` делает тест резонансов и записывает его в график подробнее [**прочитать тут**](/shaper/readme.md)

`WARMUP` данный макрос двигает печатную голову по осям икс и игрек.  Предназначен для разгона консистентной смазки по валам после процедуры смазки и теста  движений осей икс и игрек.

После этого ваша вебпанель приобретет более аккуратный вид и нужные вам макросы будут более наглядно расположены



<h2>Разные мелочи</h2>

В K1SE ставить  9 пункт "Fans Control Macros" хелпер скрипта не получится потому что нет ни заднего ни бокового вентилятора. но в этом пункте есть полезный макрос управления вентилятором обдувом материнской платы. Чтобы он у нас заработал достаточно открыть `printer.cfg` в свободном месте вставляем следующий блок:

```
[duplicate_pin_override]
pins: PC6, PB2, ADC_TEMPERATURE

[temperature_fan soc_fan]
pin: PB2
cycle_time: 0.0100
kick_start_time: 0.5
hardware_pwm: false
max_power: 1
shutdown_speed: 0
sensor_type: temperature_mcu
min_temp: 0
max_temp: 100
control: watermark
max_delta: 2
target_temp: 45.0
max_speed: 1.0
min_speed: 0.0
tachometer_pin:PC6
```
Не забываем сохранить и перезапустить конфигурацию.   По итогу увидим так: 



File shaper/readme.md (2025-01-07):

<h3 align="right"><a href="https://www.tinkoff.ru/rm/yakovleva.irina203/51ZSr71845" target="_blank">ваше "спасибо" автору</a></h3>
<h3 align="right"><a href="https://t.me/tombraider2006" target="_blank">телеграм канал автора</a></h3>
<h5 align="right">поставьте "звездочку" проекту. так другим пользователям легче его найти.</h5>

**читаем графики шейперов**

основная статья по шейперам у меня как и раньше [расположена тут](https://github.com/Tombraider2006/klipperFB6/tree/main/accel_graph).

 Данный материал предназначен для тех, кто решает надо ли  производить расточку посадочных мест под втулки печатной головы или ему повезло.  максимально упрощенно и максимально наглядно покажу что и как делать. 

 для того чтобы произвести тест необходимо поставить [**Helper script**](https://guilouz.github.io/Creality-Helper-Script-Wiki/helper-script/helper-script-installation/) если он уже у вас установлен находим макрос `TEST_RESONANCES_GRAPHS` запускаем и дожидаемся выполнения. 
 
 После окончания теста в папке:
 
  `/Helper-Script/improved-shapers`

будут находится наши графики,  нас интересует тот, что отображает данные по икс.   как могут выглядеть плохие графики: 









Обратите внимание на **голубую** линию которая обозначает кривую резонансов *после*  применения шейперов на всех вышеперечисленных графиках мы видим ярко выраженный пик в районе 12-17 герц.  это означает что вам необходимо провести работы со втулками оси икс 

<details><summary>Как вылечить клин Х</summary>
Основная проблема принтеров Creality серии K1 и её устранение.
Немного теории: "голова" принтера перемещается по оси X на двух круглых полых валах. Для плавного и тихого скольжения используются две бронзово-графитные втулки. 
Нижняя втулка установлена в голове неподвижно, а верхняя для компенсации небольшой несоосности валов (при ограниченных бюджете и массе прецизионная конструкция невозможна) - с так называемой "плавающей" посадкой. Канал под втулку имеет слегка овальное сечение, поэтому она имеет возможность немного изменять положение своей оси.
Чтобы втулка не вылетела из головы, она ограничена по бокам (но не зажата намертво!) двумя шурупами.
Чтобы голова не болталась на плавающей втулке - та поджата спереди двумя пружинами. 

Суть проблемы: внутри  канала верхней втулки есть литьевой дефект: внутрь торчит горбик (примерно посередине канала) и заклинивает втулку.
Вдобавок к этому два торцевых шурупа при закручивании также выдавливают пластик внутрь канала, и он поджимает втулку.

Что делать:
Работаем только с верхней, нижнюю втулку не трогаем, её канал строго круглого сечения и она в нём плотно запрессована, двигаться не должна.

Снять кожух обдува с головы, отсоединить прижимной кронштейн с кабелем (под ним 2 пружины - не потеряйте), выкрутить два  шурупа, ограничивающие втулку по бокам, и выдавить её в сторону (иногда это совсем непросто - сразу мешает дефект). 
Оправка, пригодная как для выталкивания втулки, так и для расточки головы: https://www.printables.com/model/1022787-tool-for-modifying-the-x-axis-carriage-for-k1-k1c
Наклеить на оправку полоску  шкурки 500 гридности ( https://www.ozon.ru/product/nazhdachnaya-bumaga-vodostoykaya-sia-shkurka-shlifovalnaya-p500-nazhdachka-280x230-mm-628624774/ ) и  вращательно-поступательными движениями аккуратно сточить 3 проблемных точки.
Втулка в итоге должна свободно заходить в канал, пальцем навылет.
Главное не переусердствовать! Пара человек уже так расточила, что всё болтаться начало.

Внутренности втулок промываем от остатков старой смазки и загрязнений следующим способом: вытираем валы насухо, например, бумажными салфетками, капаем по одной капле жидкого машинного масла на вал, раскатываем, двигая голову вправо-влево. Снова вытираем и повторяем. 

Для валов оси X с медно-графитовыми втулками рекомендуется жидкое машинное масло, типа И-20А или иное, например, для швейных машинок. Достаточно 1 капли на каждый вал. Из-за малого зазора между втулками и валами густая смазка будет тормозить движение и портить шейперы. 

Также можно попробовать(но не обязательно) заменить 2 штатные прижимные пружины на более мягкие (10 мм длиной, 4,7 мм диаметром, проволока 0,5 мм): https://www.ozon.ru/product/pruzhina-szhatiya-dlina-l-10-mm-shirina-d-4-7-mm-diametr-provoloki-d-0-5-mm-10-sht-v-upakovke-1009309923/
</details>

Как выглядит график у тех кто провел операцию по устранению и у тех, кому повезло купить принтер без косяков и не игнорировать смазку осей.







 P.S. 
  в данном руководстве не рассматриваются конкретные значения ускорений. графики рассматриваются исключительно по кривым резонансов и служат для демонстрации возможных проблем и их решений.

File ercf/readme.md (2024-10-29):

<h3 align="right"><a href="https://www.tinkoff.ru/rm/yakovleva.irina203/51ZSr71845" target="_blank">ваше "спасибо" автору</a></h3>
<h3 align="right"><a href="https://t.me/tombraider2006" target="_blank">телеграм канал автора</a></h3>

Постройка и настройка многоцветной печати на базе принтера К1\К1С\К1MAX.

Первое, перед тем как вы встаненте на этот путь поймите что это не законченный продукт, это проект. поэтому какие то решения будут меняться со временем. 

1. покупка набора.

     На момент написания было несколько основных производителей наборов это "Blurolls" "Fisetс" и "Siboor" Последнего выгодно отличает первого набора наличие фрезерованной шестерни которую очень непросто изготовить, а также уже подготовленной 3 платы с уже монтированными диодами и концевиками что избавит от муторной пайки и наличие уже готовых обжатых подписанных жгутов проводов чем отличается от "Fisetc". плата управления в "Fisetc" своя фирменная ERB Fysetc. в наборе "Siboor" BTT MBB _ ERB v2,0  которую отличают хорошие сьемные драйвера и наличия бОльшего количества разьемов. есть еще набор от "Triangl labls" детали там качественные но нет платы управления, детали россыпью, паять придется и обжимать на порядок больше. и только Blurolls продает полный комплект с печатными деталями, которые очень низкого качества. 

    > Сколько нитей филамента
    
     будет в вашем наборе 6 8 или 12. не стоит хапать исключительн по принципу больше лучше, вам это все еще настраивать и чем длиннеее ряд деталей тем больше ошибок может набраться. 

    > Печатные детали.
    
     Покупать или изготавливать самостоятельно каждый решает сам, могу лишь посоветовать смотреть фотографии продавца самих печатных моделей, на том же AliExpress есть масса продавцов которые продают с настолько ужасным качеством что я бы им и тестовый куб не доверил печать не то что детали которые требуют повышенной точности, а точность понадобиться так как многие детали вставляются одна в другую и не только.  

    Рекомендуемый набор Siboor [**AliExspress**](https://aliexpress.ru/item/1005006724753869.html) не только собраны все нужные детали но и распределены по коробочкам подписанным что облегчает процесс сборки.

    1.1 Дополнительные платы и наборы.

    > [**Seleadlab Серворезак Полный комплект для ERCF V2**](https://aliexpress.ru/item/1005006964064173.html) необходим для подрезания нити филамента.

    >Мануал по его установке тут?? 

    > **Платы управления.**

    **Orange Pi 3 lts** в качестве хоста  для програмного обеспечения а также для подключения экрана [**AliExspress**](https://aliexpress.ru/item/1005003577312703.html) и сразу радиаторы охлаждения к ней [**берем тут**](https://aliexpress.ru/item/1005004139227052.html)

    > **Экран** 
    
    К сожалению не получится на родном экране креалити реализовать управление над сменой филамента. 
    чем больше экран тем лучше. [**Aliexpress 10"**](https://aliexpress.ru/item/1005004016097549.html)  [**Aliexpress 7"**](https://aliexpress.ru/item/1005003151617679.html)

2. Сборка.

    > Мне понравилось серия видео от одного англоязычного пользователя. [**YouTube**](https://www.youtube.com/watch?v=SErkD0USpGs&t=7s)

3.

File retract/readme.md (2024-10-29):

<h3 align="right"><a href="https://www.tinkoff.ru/rm/yakovleva.irina203/51ZSr71845" target="_blank">ваше "спасибо" автору</a></h3>
<h3 align="right"><a href="https://t.me/tombraider2006" target="_blank">телеграм канал автора</a></h3>
<h5 align="right">поставьте "звездочку" проекту. так другим пользователям легче его найти.</h5>

<h2> управляем ретрактом во время печати.</h2>

в прошивке клиппер возможно управлять ретрактом во время печати. это нужно если вы внезапно увидели, что ваш пластик отсырел и начал тянуть сопли,  а у вас уже прошло "n" часов печати и так лень все начинать заново. но для этого нужно немного подготовительной работы. 

первое. в орке заходим в настройки принтера и ставим галки "использовать откат из прошивки" 



далее в стартовом коде принтера добавляем блок:

```
SET_RETRACTION RETRACT_LENGTH=[retraction_length] RETRACT_SPEED=[retraction_speed] UNRETRACT_EXTRA_LENGTH=[retract_restart_extra] UNRETRACT_SPEED=[deretraction_speed]
RESPOND TYPE=command MSG="Retraction length set to [retraction_length]mm" 
RESPOND TYPE=command MSG="Retract speed set to [retraction_speed]/[deretraction_speed]mm/c"
```


не забывайте вписывать значение отката для своего пластика когда настраиваете.

например так:



далее переходим в принтер и открываем файл printer.cfg

вписываем такой раздел:

```
[firmware_retraction]
retract_length: 0.43 # безопасное значение для того пластика которым чаще всего печатаете.
retract_speed: 30
unretract_extra_length: 0
unretract_speed: 30

```
после перезагрузки если вы не увидели нового раздела в правом верхнем углу тыкаем в три точки и ищем следующий раздел:



внутри находим раздел "настройки отката" и ставим галочку



В результате у нас появится новый раздел в веб панели с помощью которого вы можете прямо во время печати управлять вашим ретрактом. 



проверить все ли у вас правильно перед печатью можно нарезав модель и сохранив ее на диск, далее открываем файл с помошью текстового редактора и ищем `START_PRINT` 



убеждаемся что у нас есть команда **set_retraction** и то что там у нас цифры, а так же что дальше у нас есть команда **G10**  которая означает что послана команда на ретракт который будет обработан прошивкой.

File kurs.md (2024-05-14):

О КУРСЕ
Этот курс – необходимый компаньон для тех, кто только начинает свой путь в мире 3D-печати. Чтобы не утонуть в океане информации требуется наставник, способный ориентировать вас в огромном объеме материалов.

Именно здесь я приду к вам на помощь, предлагая не только основы, но и ключевые ссылки на актуальные и релевантные источники.

Мой курс разработан так, чтобы помочь вам быстро освоить все тонкости работы с 3D-принтерами, предоставив полезные сведения и сократив путь к вашему профессиональному росту.  

 настроим слайсер, на принтер К1\Кмакс\K1C поставим модифицированную прошивку со всеми новыми наворотами. 

 1. Установка модификаций ПО
 2. Тонкая настройка конфигурационных файлов принтера
 3. Пояснение принципов работы и каждого изменения от стокового ПО
 4. Обьяснение нюансов интерфейса веб панели и его практического применения
 5. Советы по регулярному обслуживанию принтера.
 6. Cоветы по исправлению наклона стола.
 7. Интерфейс слайсера и настройка под принтер.
 8. Объяснения настроек параметров пластика.
 9. Порядок тестов настройки параметров пластиков и нюансы проведения тестов.
 10. Пробная печать, пояснения особенностей алгоритмов работы. на том пластике который у вас есть(pla, petg, ABC)
 11. Ответы на вопросы по печати.   
 
  в общем  провожу вас за ручку в мир качественной быстрой печати. 
записаться можно тут(пишите ник в телеграмме) 

https://easyweek.ru/tom-tomich

 [**видеоотзыв по обучению**](https://youtu.be/q9dPGSkCr6M?si=31thqjn6EUDBIXiD)

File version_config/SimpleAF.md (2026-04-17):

[↩️ Назад в главное меню](../readme.md)

---

# 🚀 Обзор и быстрый старт прошивки Simple AF

> Продвинутый вариант прошивки - для этого варианта необходимо докупить датчик по Z

<h3 align="right"><a href="https://www.tinkoff.ru/rm/yakovleva.irina203/51ZSr71845" target="_blank">💝 Поддержать автора</a></h3>

---

## 📑 Оглавление

- [📖 Введение](#-введение)
- [⚡ Проблемы стоковой прошивки](#-проблемы-стоковой-прошивки)
- [✨ Плюсы Simple AF](#-плюсы-simple-af)
- [🎯 Варианты датчиков](#-варианты-датчиков)
- [🔧 Установка](#-установка)
- [📝 Настройка слайсера](#-настройка-слайсера)
- [💡 Полезные макросы](#-полезные-макросы)
- [🎓 Нужна помощь?](#-нужна-помощь)

---

## 📖 Введение

Время не стоит на месте и вместо Helper Script призванного заштопать очевидные дыры на старте продаж линейки К1 приходят более объемные и кардинальные решения.

**Цель этой статьи:** Рассказать зачем нужна прошивка [**Simple AF**](https://pellcorp.github.io/creality-wiki/), какие плюсы и как быстро начать с ней работать.

---

## ⚡ Проблемы стоковой прошивки

Данная модификация призвана решить несколько проблем существующих на стоковой прошивке и не устранимых даже с модификациями Helper Script:

### 1. Долгий старт и неточное тестирование

Первоначальный тест Z оси, очистка сопла, "круг почета" тестирования тензодатчиков. В прошивке Simple AF родные тензодатчики не задействованы - вместо них предлагается использовать альтернативы.

### 2. Ограничение алгоритма KAMP

Из-за кривого написания модуля тензодатчиков алгоритм работает только с сетками 3×3, 4×4, 5×5 и так далее. Назначить сетку больше чем 6×6 тоже бывает проблематично.

### 3. Отсталость от современных тенденций

Алгоритм Input Shaping, Adaptive Mesh и еще многое получило свое развитие, в отличии от прошивки которая находится в том же состоянии что и несколько лет назад! 

Косметические улучшения не устранили отставание, а где-то и привнесли новые проблемы. *Например в новых прошивках распространяемых с модом SFC kit вырезаны функции команды git, которые затруднили установку модифицированного софта*

**Всё это мы вынуждены терпеть из-за выбора компанией Creality собственного пути развития датчиков оси Z который разошелся с основной веткой Klipper.**

---

## ✨ Плюсы Simple AF

Немного с сайта прошивки о плюсах данного решения:

1. ✅ **Открытый исходный код** - Simple AF использует ПО с открытым исходным кодом, и весь его исходный код открыт

2. ✅ **Простая конфигурация** - все макросы и конфигурации находятся в каталоге config и доступны вам, ничего не заперто в закрытых исходных кодах

3. ✅ **Обновленный Klipper** - используемая нами версия Klipper, хотя и является ответвлением от основной версии, регулярно обновляется с помощью Klipper3d, и никакие наши добавления не меняют базовое поведение Klipper

На сайте Simple AF вы можете прочитать об установке различных вариантов прошивки и **главное что вам надо выбрать** - это вариант замены тензодатчиков стола, которые не поддерживаются современной версией Klipper.

---

## 🎯 Варианты датчиков

### ⚠️ Важная рекомендация

**Я рекомендую не смотреть на варианты** `microprobe`, `Klicky`, `Bltouch` если вы гонитесь за скоростью. Алгоритм не сильно будет отличаться от варианта с тензодатчиками стола *(подъехай-померяй высоту в точке)*.

### Контактные датчики (медленные):

#### 1. BLTouch
- ✅ Самый дешевый / не требующий больших усилий вариант установки прошивки
- ❌ Самый неточный (можно взять датчик собранный в подвалах бескрайнего Китая)

#### 2. Klicky
- ✅ Дешевый
- ⚠️ Требует времени и прямизны рук
- Точность сильно зависит от качества сборки
- Немного отбирает рабочее пространство стола

#### 3. Microprobe
- ✅ Брендовый датчик
- ✅ Большая точность
- ❌ Но в большинстве случаев такая точность не нужна
- ❌ Тесты будут долгими
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

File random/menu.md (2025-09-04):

<h3 align="right"><a href="https://www.tinkoff.ru/rm/yakovleva.irina203/51ZSr71845" target="_blank">ваше "спасибо" автору</a></h3>
<h3 align="right"><a href="https://t.me/tombraider2006" target="_blank">телеграм канал автора</a></h3>

<h1>Пункты меню хелпер скрипта.</h1>

Целью этого руководства является не перевод как таковой, а пояснение того, что не всегда очевидно простому пользователю.
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

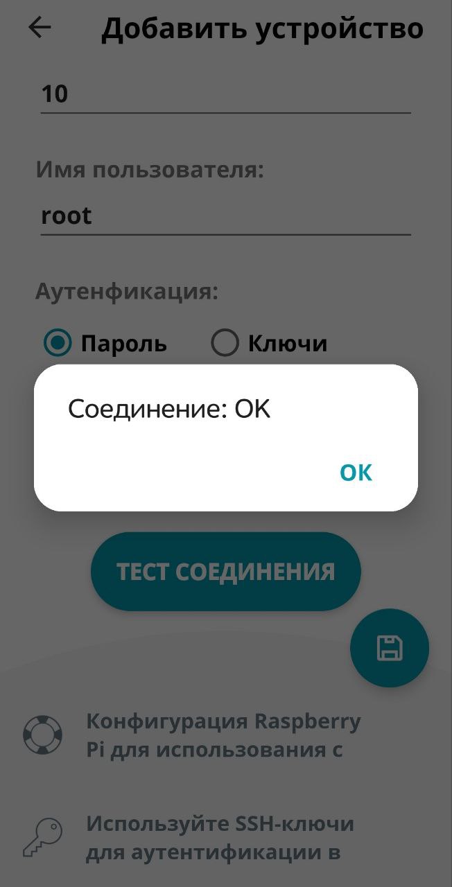
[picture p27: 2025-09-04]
random/images/rasp4.jpg

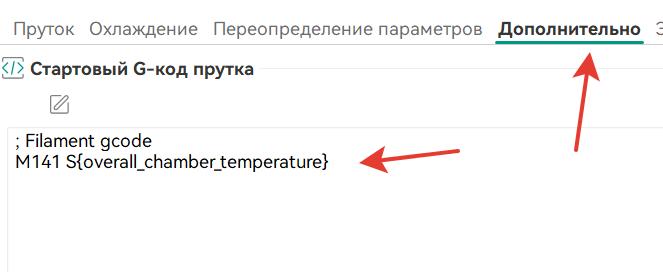
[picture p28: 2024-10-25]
random/images/temp_settings2.jpg

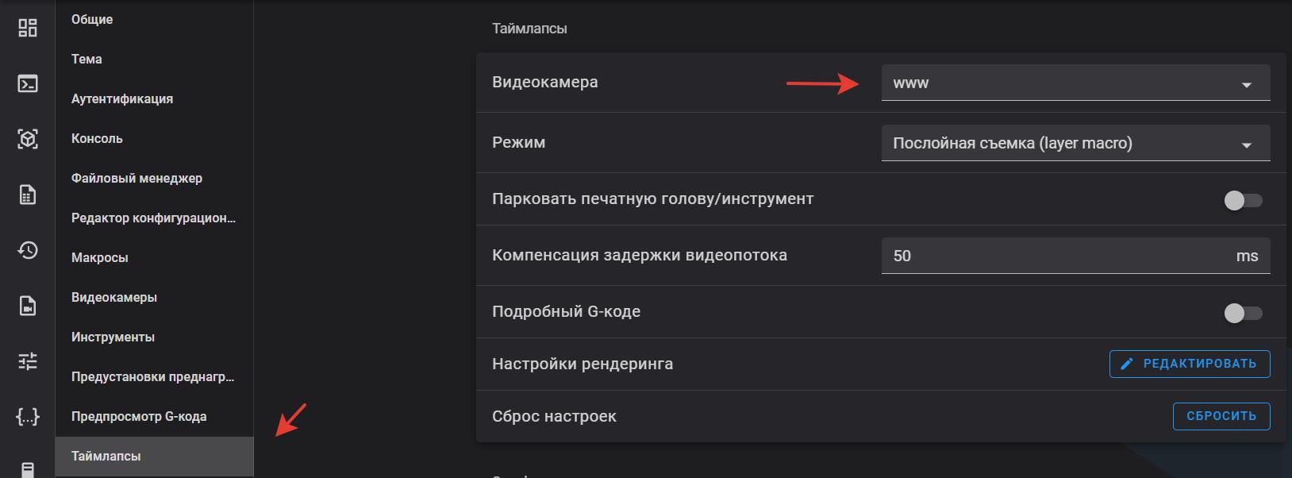
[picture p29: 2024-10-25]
random/images/timelapse1.jpg

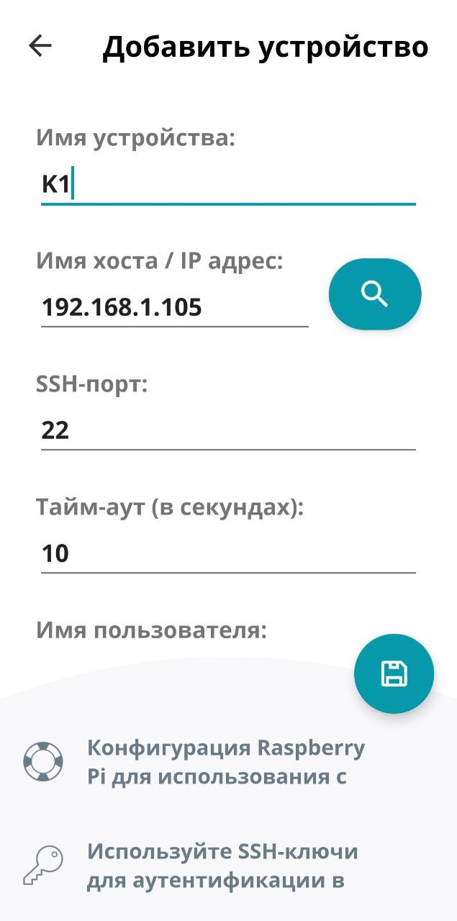
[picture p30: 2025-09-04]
random/images/rasp2.jpg

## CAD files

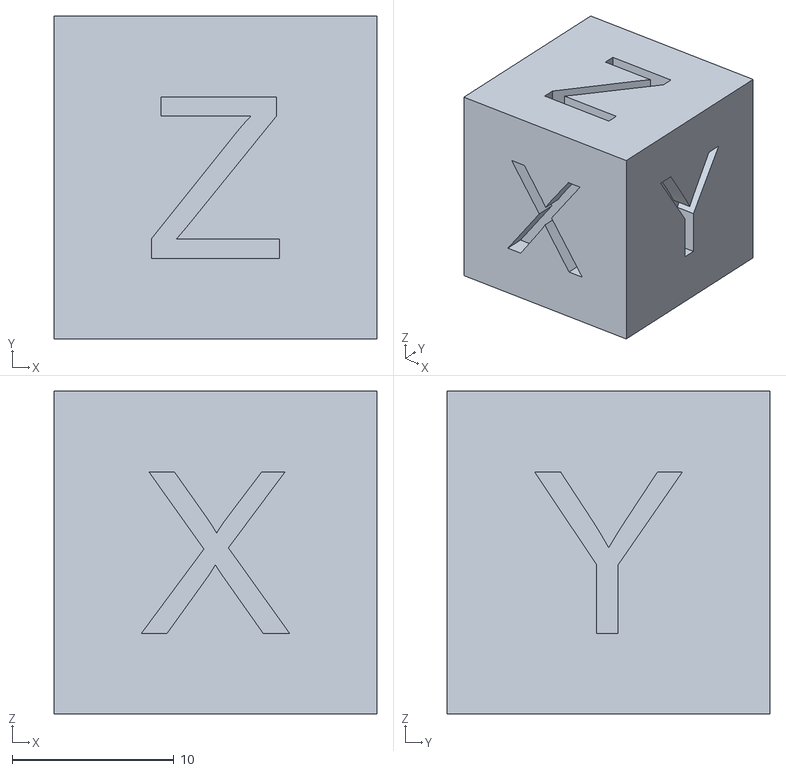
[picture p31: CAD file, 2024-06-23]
extras/Cube.stl
20.0 x 20.0 x 20.0

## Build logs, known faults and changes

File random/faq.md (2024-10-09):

Q: **Как смазывать принтер?**
A: Перед смазкой принтера ОБЯЗАТЕЛЬНО уберите магнитную пластину или накройте стол несколькими слоями газеты! Масло точно будет капать вниз и оно может не отмыться со стола. Ремни смазывать не надо! Избегайте попадания смазок на ремни, масло может привести к их повреждению.

Ось X - смыть с валов старую смазку растворителем (спиртом), затем нанести на вал маленькое количество жидкого машинного масло (для швейных машинок, либо что-то похожее на И-20А) и распределить по всей длине. Оптимальнее всего отвести голову в один конец до упора, накапать на оба вала масло прямо перед головой, увести голову в другой конец до упора, снова накапать на оба вала масло прямо перед головой, и провести из конца в конец голову несколько раз чтобы масло распределилось равномерно.
Если где-то по ходу движения головы заедает, можно нанести масло в эту конкретную точку, и так же распределить
Если видите, что после нанесения масла под втулкой остаётся чёрная жижа - это масло смешалось с угольной пылью из втулки, протрите салфеткой и добавьте ещë масло на замену. Ацетон в качестве растворителя использовать можно, но следите, чтобы он ни в коем случае не попал на пластиковые части печатной головки - разъест. Лучше использовать спирт.

Ось Y, Z - рекомендуется заполнить линейный подшипник адгезионной смазкой (смазка для петель автомобильных дверей). Сквозь зазор у сальника впрыснуть в принципе реально. Можно нанести на сам вал и очень долго катать по нему подшипник, пока смазка не покроет все шарики. Также можно использовать смазку из комплектного тюбика.
Для приводных винтов также можно использовать адгезионную смазку, можно использовать литол или другую литиевую смазку, но обратите внимание, что и то, и другое ОЧЕНЬ сильно пачкает руки.

Q: **502 mainboard fan exception. Ошибка 502 вентилятора материнской платы во время печати**
A: по пунктам, когда вы ставите пункт 9 Fans Macros Control вы меняете логику нескольких вентиляторов. первое, именно с моей подачи у нас теперь сам принтер может регулировать температуру в камере. я объеденил температурный датчик и задний вентилятор и теперь возможно выставить температуру печати.

Второе и главное, с моей подачи ребята пошли дальше и сменили логику вентилятора материнской платы Soc Fan . раньше логика была следующая - если работают моторы икс и игрек значит работает вентилятор обдува материнки. теперь она по умолчанию 45 дельта 2 - при достижении температуры 47 градусов включается вентилятор материнской платы 45-2 то есть 43 градуса он выключается. однако где то в глубине китайских скриптов есть макрос который во время печати проверяет работает ли кулер. и когда обнаруживает что нет, (ну а зачем собственно?) он пишет предупреждение на экране принтера "Ошибка вентилятора материнской платы" что с этим делать? да забить и не париться. ибо у нас все прекрасно и хорошо и мы спокойней спим так как ресурс кулера увеличился, принтер на несколько процентов стал тише, а что он там пишет да бог с ним.

Q: **Можно что-то сделать с кабельной цепью, которая постоянно щёлкает, когда печатная головка оказывается слева?**
A: Есть два вариант - поднять конец цепи со стороны печатной головки (это также упростит снятие её крышки), или заменить цепь полностью на кабельный рукав "змеиная кожа".

Q: **При загрузке пластика он очень плохо заходит в фидер, приходится постоянно отстёгивать трубку, а печати композитами пруток заламывается на входе в фидер, что делать?**
A: Это всё виноват очень крутой изгиб тефлоновой трубки, но по другому её не проложить, т.к. она упирается в крышку принтера. Для исправления ситуации надо сделать так, чтобы крышка была выше. Для этого есть так называемые "райзеры".
Отдельно стоит упомянуть версию райзера, которая позволяет не только распрямить тефлоновую трубку, но и переместить сенсор филамента и кабельный жгут повыше.
В основной группе есть несколько разных райзеров, здесь прикреплю несколько ссылок на разные версии одного, который хорошо себя зарекомендовал:
* Сам райзер: https://www.printables.com/model/545370-creality-k1-k1-max-riser
* Вариация с перемещением сенсора: https://www.printables.com/model/665955-creality-k1-max-riser-improved-filament-path-k1-ad
* Вариация для новых ревизий K1 Max: https://www.printables.com/model/939647-k1-max-riser-corner-piece-for-newer-revisions

В ремиксах у каждой из них вы можете найти нужные вам модификации.

Q: **Дверца открывается только на 90 градусов и очень нехорошо стоит в открытом положении, страшно случайно надавить на неё и разбить**
A: Петли дверцы можно заменить на печатные, открывающиеся на 270 градусов.
Есть несколько вариантов, я настоятельно рекомендую вот этот: https://www.printables.com/model/735524-creality-k1k1ck1-max-door-hinges-geared
Для печати обязательно использовать версию с зазором 0.2, слой 0.2 миллиметра и обязательно переключить движок с Arachne на классический (в противном случае шестерни и оси склеиваются между собой прямо в слайсере).

Q: **Принтер дребезжит при печати, особенно сильно слышно при калибровке шейперов, что делать?**
A: Дребезжит сильнее всего нижняя панель. Её можно полностью снять (Сначала напечатайте рамку для вентилятора от Henlor - https://www.printables.com/model/540070-motherboard-fan-mount-mk2-collection-creality-k1-s/files), а можно проклеить по периметру рамы под ней уплотнительную ленту (можно тканевую антискрипную) и поставить обратно. Если дребезг не ушёл полностью, попробуйте ослабить все винты на боковых панелях и затянуть их все обратно.

Q: **При печати первого слоя заметно, что карта стола неточная - где-то принтер пытается печатать дальше чем надо от стола, как это исправить?**
A: К сожалению, это дефект обработки тензодатчиков стола, который не исправить только программными методами. Потребуется установка тензомода, которому посвящена группа [тензомода.](https://t.me/K1_Tenso_Mod/1619) К сожалению, в отличие от остальных модификаций, перечисленных в данном разделе, для установки этой модификации требуется большое количество навыков, включая пайку, исправление конфигов и работу с Linux, так что это мод "не для всех".

Q: **Что такое хелпер скрипт? Как устанавливать Fluidd?**

*Замечание: Здесь и далее будет выполняться работа с консолью Linux (командной строкой, терминалом). Консоль Linux и консоль Klipper - это две разные консоли, и во избежание путаницы везде будет явно указано, в какой момент с какой из них будет выполняться работа. Описанные здесь действия не являются заменой прошивки и не влияют на её работу. Тем не менее, для выполнения этих действий потребуется получение ROOT-доступа к принтеру (делается через экран). При работе с консолью Linux все надписи будут только на английском языке. В данной инструкции будут представлены переводы и описания для надписей, относящихся к основным действиям, однако, ожидается, что вы можете самостоятельно понять надпись или найти перевод.*

A: Для полноценной работы ряда функций, которые обычно ожидаются от такой продвинутой прошивки как Klipper, на принтерах Creality потребуется установка дополнительного ПО. Однако, следует учитывать, что принтер работает под OS Linux, на которой установка ПО сильно отличается от таковой под Windows, и может являться нетривиальной задачей. Для упрощения операций по установке был написан специальный скрипт-помощник (хелпер-скрипт), который поможет избавить вас от ошибок при выполнении тех или иных действий. Инструкция по установке хелпер-скрипта на английском языке представлена здесь: https://github.com/Guilouz/Creality-Helper-Script-Wiki/blob/main/docs/helper-script/helper-script-installation.md, а в данной инструкции будет представлен адаптированный перевод на русский язык.

В первую очередь, потребуется получить доступ к консоли Linux вашего принтера. Для этого нужно на экране принтера перейти в меню настройки и разблокировать Root-доступ. Без этого получить доступ к консоли невозможно. Разблокировка Root-доступа запустит на принтере SSH-сервер, к которому мы и будем подключаться. Помимо этого, на экране будут отображены логин и пароль для подключения (Это всегда логин root и пароль creality_2023)

Для подключения вам потребуется SSH-клиент на вашем ПК. Под Windows удобным клиентом является программа PuTTY (https://www.putty.org/). Также можно подключиться со смартфона Android, используя клиент Juice SSH из Google Play. Если вы используете Linux или MacOS, вы и так знаете, как установить SSH-клиент и подключиться к принтеру. Для подключения вам нужно будет ввести IP-адрес принтера, а после появления чёрного окна консоли - логин и пароль (описаны выше). Теперь у вас есть доступ к консоли Linux вашего принтера.

Установка хелпер-скрипта выполняется вот такими двумя командами в этой консоли (обратите внимание, что комбинация клавиш Ctrl+V в окне консоли не работает, но можно выполнить вставку нажатием на колёсико мыши, через контекстное меню или комбинацией Shift+Insert):

```
git config --global http.sslVerify false
git clone https://github.com/Guilouz/Creality-Helper-Script.git /usr/data/helper-script
```

Можно скопировать обе команды разом в консоль, после этого нажмите Enter.
Теоретически, первая команда не является обязательной и установка должна пройти нормально без этого, но в последнее время участились жалобы на ошибки при клонировании, которые исправляются первой командой

Если всё пройдёт успешно, хелпер-скрипт установится в папку /usr/data/helper-script на принтере. Запустить его можно командой:

```
sh /usr/data/helper-script/helper.sh
```

После запуска откроется меню, в котором можно выбрать, что требуется сделать.

Список программ, доступных для установки, иногда изменяется, поэтому не следует полагаться на актуальность представленного здесь скриншота.

Ниже будет кратко перечислено, какой из пунктов для чего нужен.

**1 - Moonraker.**

 Это HTTP API для Klipper, позволяющее отправлять файлы на принтер напрямую из слайсеров (Prusa, Orca), добавив в слайсер физический принтер с указанием IP-адреса и порта 7125 (порт указывается через двоеточие).

**2 или 3 - Fluidd и Mainsail** - это веб-интерфейсы для Klipper, позволяющие полноценно управлять принтером через браузер. Обычно при установке Klipper подразумевается наличие одного из них как основного метода управления принтером. Они взаимозаменяемы между собой, можно выбрать любой (в инструкциях ниже будет использоваться Fluidd). Одна из полезнейших вещей, которые предоставляют веб-интерфейсы - доступ к редактированию файлов конфигурации и макросов.

Веб-интерфейсы после установки не знают о наличии в принтере веб-камеры, её нужно добавить в настройках.

**4 - Entware** - это пакетный менеджер для установки программ (здесь уже именно программ). Для пользователей, знакомых с Ubuntu - это аналог apt, запускаемый через команду opkg. Он нужен для некоторых из идущих ниже пунктов, скрипт попросит вас установить Entware при необходимости - просто так его ставить не нужно.

**5** - Функционал для запуска команд Linux из макросов Klipper. Он нужен для работы спикера (Buzzer) и графиков шейперов.

Идущие ниже пункты раздела Improvements - это различные макросы. Самые полезные из них - это KAMP и Improved Shapers.
**6 - KAMP** - один из самых полезных пунктов в списке, если у вас установлена стоковая прошивка: Адаптивное измерение карты стола, позволяет ускорить начальную подготовку к печати. KAMP будет считывать список объектов из файла G-кода и измерять карту стола только вокруг перечисленных там объектов.
Для пользователей тензомода с чистым клиппером, в "полноценном" Klipper не от Creality вместо KAMP есть Adaptive Bed Mesh
Для работы этой функции нужно включить описание названий моделей в слайсере (настройки печати - выходные параметры - Название моделей - "Зависит от типа прошивки")

**7 - Поддержка спикера (Buzzer - команды BEEP)**. Позволит принтеру издавать писк по команде. В последних партиях К1с спикер был не распаян, в них может не заработать.

**8 - ускорение старта печати** небольшое ускорение старта за счет оптимизации макроса. 

**9 - изменение логики кулеров** обьединение датчика температуры с задним вентилятором дает возможность контролировать температуру внутри камеры.  SocFan это изменение логики вентилятора обдува материнской платы. по умолчанию он включается как только становятся активными моторы икс и игрек.  после изменения можно регулировать температуру с дельтой 2 - тоесть когда стоит температура 45 кулер включится при достижении 47 градусов и отключится при достижении 43 градусов. 

однако  где то в глубине китайских скриптов есть макрос который проверяет работает ли этот кулер во время печати и если в этот момент он не работает выдает на экран "ошибка вентилятора материнской платы" что можно смело игнорировать.
 
**10 - Improved Shapers** - Улучшенные макросы для упрощения калибровки шейперов а так же механизм и библиотеки необходимые для создания графиков (Input Shaping).

**12 - Save Z-Offset Macros** - Макросы для настройки и сохранения на ходу значения Z-Offset (настройка зазора сопла от стола). В стоке предполагается, что карта стола строится идеально и настройка этого зазора из интерфейса не предусмотрена. Есть способы обойтись без этого макроса, будут описаны ниже.

Пункт 13 (Screws Tilt Adjust) не работает на принтерах серии K1, он нужен для Ender 3 KE

**16 - Moonraker Timelapse** - Функционал таймлапсов (интервальной съёмки), который будет доступен из Fluidd. Обратите внимание, что хоть он и повторяет функционал таймлапсов от Creality, они не связаны между собой, и настроить таймлапсы Creality (равно как и скачать видеозаписи тех таймлапсов) через Fluidd невозможно. Перед использованием рекомендуется настроить позицию парковки и параметры ретрактов. Также, напоминаю, что сразу после установки веб-интерфейсы не знают о наличии веб-камеры в принтере, и её нужно добавить в настройках.
Не ставьте позицию парковки для таймлапсов в задние углы! В тех координатах (как минимум на модели Max) голова врезается в двигатели и происходит непостоянное смещение слоёв, которое сложно диагностировать. Оптимальные координаты - сзади по центру (150:300 на Max).

**Раздел Remote Access** - это различные варианты удалённого доступа к принтеру. Обратите внимание, что если вы пытаетесь установить GuppyScreen, то он находится в ДРУГОМ разделе, а GuppyFLO из раздела удалённого доступа никак с ним не связан.

Q: **При печати заметна явная недоэкструзия между 2 и 10(5-50) миллиметрами по координате Z, близко к центру стола, при этом ближе к краю и выше по Z такой проблемы нет**
Либо, наблюдается переэкструзия на этой высоте ближе к краю, при этом по центру всë в порядке

Для исправления требуется доступ к файлам конфигурации - см. выше

A: Такая проблема может вызываться плохо откалиброванным коэффициентом PA. Если это так, то она будет проявляться на случайных высотах, с переэкструзией на коротких линиях.
Если же она проявляется только на указанной высоте независимо от модели, это - результат компенсации экструзии алгоритмом Fade, выравнивающего высоту печати согласно карте стола. К сожалению, этот алгоритм работает из предположения, что оси XY не провисают, и карта показывает исключительно неровности стола, а на принтерах серии K1, помимо неровности стола, на карту также влияет провисание валов под весом механики, больше всего заметное в виде бугра по центру оси Y, идущего вдоль оси X. Больше проявляется на принтерах K1 Max, т.к. там валы длиннее и провисают глубже.

Решение проблемы здесь состоит в отключении алгоритма Fade. Однако, перед этим, необходимо убедиться, что углы на карте стола стоят на одной высоте - настолько, насколько возможно.
Для отключения нужно в файле конфигурации `printer.cfg` в секции `[bed_mesh]` найти параметр `fade_end` и установить его значение в 0.

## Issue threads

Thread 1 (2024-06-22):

фирмваре ретракшин

Barconero, 2024-06-22:
у вас указано в профиль **филамента** вписывать код
`SET_RETRACTION RETRACT_LENGTH=[filament_retraction_length] RETRACT_SPEED=[filament_retraction_speed] UNRETRACT_EXTRA_LENGTH=[filament_retract_restart_extra] UNRETRACT_SPEED=[filament_deretraction_speed]`

это не оптимально - нужно будет перезаписать все профили.
гораздо проще один раз в профиле принтера казать:
`SET_RETRACTION RETRACT_LENGTH=[retraction_length] RETRACT_SPEED=[retraction_speed] UNRETRACT_EXTRA_LENGTH=[retract_restart_extra] UNRETRACT_SPEED=[deretraction_speed]
RESPOND TYPE=command MSG="Retraction length set to [retraction_length]mm"
RESPOND TYPE=command MSG="Retract speed set to [retraction_speed]/[deretraction_speed]mm/c"`

тогда подхватятся все переопределения, а если их не было возьмутся значения из профиля принтера

Tombraider2006, 2024-06-22:
спасибо, да. действительно должно получится лучше. как проверю, добавлю в мануал.

Closed 2024-07-30.

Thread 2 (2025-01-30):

can we use the pico to controle a 24v fan  auxiliar fan in my printer

ducati1198, 2025-01-30:
hello, im testing out your pico projet, i will like to control a 24v auxiliar fan. the reason why is my printer motherbord as only one 24v 1A pinout and it already max out from the factory fan (creality k1 max) do you know any way of controling the the fan speed with a pico

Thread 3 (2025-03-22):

Установка последнего клиппера не работает на K1SE

Olegaas, 2025-03-22:
>>>порядок установки если вам нужен более новый клиппер

Проделал операцию на 2-х K1SE - неправильно работает экран. Не отображает температуры (все=0), движения и т.д. Очень похоже, что нет связи с главной платой. Сброс на заводские параметры работает.
Пробовал конфиг править из старого - ничего не получается к сожалению.
Ставить от К1С тоже пробовал - результаты одинаковые.

Нужен рабочий конфиг по ходу..

Tombraider2006, 2025-03-22:
данное обновление корректно работает только с гуппи скрином.

Closed 2025-05-03.

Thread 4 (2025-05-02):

Замена моторов

artem-sedykh, 2025-05-02:
Привет!
Спасибо за труд!
А можно подробней про

> замена моторов в моделях к1 вместе со шкивами например на [такие](https://aliexpress.ru/item/1005004731197516.html) позволяет чуть снизить шум(не доказано) и чуть снизить рябь относительно родных моторов(процентов на 20-30 меньше)

Заказал эти моторы, а у них длина другая, если не сложно поделись ифой как их менять=)

artem-sedykh, 2025-05-03:
> > Заказал эти моторы, а у них длина другая
>
> за длину моторов не переживай и за длину штока тоже. но напомню что это относится к первым ревизиям к1 на к1с на к1а это уже неактуально. если стоят 40зубыше шкивы тогда можно заморачиваться если 20 зубые смысла в этой процедуре практически нет.

Понял, спасибо!

Closed 2025-05-03.

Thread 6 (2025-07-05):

1.3.3.46 + last Klipper + NEW Input Shaping = не рабочая система

Salavat-S, 2025-07-05:
Если на прошивке 1.3.3.46 установить Helper Script по Вашей инструкции, и использовать "порядок установки если вам нужен более новый клиппер",

то установка "Новый алгоритм измерения Input Shaping" приводит к неработоспособности системы.
Выходит ошибка :

```
Internal error during connect: 'void(*)(struct trapq *, double, double)' expects 3 arguments, got 2
Once the underlying issue is corrected, use the "RESTART" command to reload the config and restart the host software.
Printer is halted
```

Closed 2025-07-06.

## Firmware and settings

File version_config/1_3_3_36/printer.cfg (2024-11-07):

# K1
# Printer_size: 220x220x250
# Version: v1.0.26
# CreateDate: 2023/03/21
# Nozzle_mcu: chip: GD32F303CBT6
#             version: CR-K1-MAX-NOZZLE-V1.0.0
# Leveling_mcu: chip: GD32E230F8P6
#             version: CR-K1-MAX-LEVELING-V1.0.0
# mcu: chip: GD32F303RET6
#      version: CR4CU220812S12


[firmware_retraction]
retract_length: 0.43 # безопасное значение для того пластика которым чаще всего печатаете.
retract_speed: 30
unretract_extra_length: 0
unretract_speed: 30




[virtual_pins]
[include sensorless.cfg]
[include gcode_macro.cfg]
[include printer_params.cfg]
[include Helper-Script/timelapse.cfg]
[include Helper-Script/save-zoffset.cfg]
[include Helper-Script/useful-macros.cfg]
[include Helper-Script/improved-shapers/improved-shapers.cfg]
[include Helper-Script/fans-control.cfg]
[include Helper-Script/nozzle-cleaning-fan-control.cfg]
[include Helper-Script/buzzer-support.cfg]
[include Helper-Script/KAMP/KAMP_Settings.cfg]

[mcu]
serial: /dev/ttyS7
baud: 230400
restart_method: command

[mcu nozzle_mcu]
serial: /dev/ttyS1
baud: 230400
restart_method: command

[mcu leveling_mcu]
serial: /dev/ttyS9
baud: 230400
restart_method: command

[verify_heater extruder]
[verify_heater heater_bed]
check_gain_time: 120
heating_gain: 1.0
hysteresis: 10

[mcu rpi]
serial: /tmp/klipper_host_mcu

[bl24c16f]
i2c_mcu: rpi
i2c_bus: i2c.2
i2c_speed: 400000

[idle_timeout]
timeout: 99999999

[virtual_sdcard]
path: /usr/data/printer_data/gcodes
on_error_gcode: # добавляем чтоб пикало при ошибках
  beep
  beep
  beep

[gcode_arcs]
resolution: 1.0

[temperature_sensor mcu_temp]
sensor_type: temperature_mcu
min_temp: 0
max_temp: 100

[temperature_sensor chamber_temp]
sensor_type: EPCOS 100K B57560G104F
sensor_pin: PC5
min_temp: 0
max_temp: 125

#[duplicate_pin_override]
#pins: PC0, PC5

#[temperature_fan chamber_fan]
#pin: PC0
#cycle_time: 0.0100
#hardware_pwm: false
#max_power: 1
#shutdown_speed: 0
#sensor_type: EPCOS 100K B57560G104F
#sensor_pin: PC5
#min_temp: 0
#max_temp: 70
#control: watermark
#max_delta: 2
#target_temp: 35.0
#max_speed: 1.0
#min_speed: 0.0

[stepper_x]
step_pin: PC2
dir_pin: !PB9
enable_pin: !PC3
microsteps: 32
rotation_distance: 40 # меняем на 72 если не меняли шкивы
endstop_pin: tmc2209_stepper_x:virtual_endstop
position_endstop: 229
position_min: -5
position_max: 229
homing_speed: 36
homing_retract_dist:0

[tmc2209 stepper_x]
uart_pin:PA9
interpolate: True
run_current:1.5
hold_current:1.0
sense_resistor: 0.100
stealthchop_threshold: 0
uart_address:3
diag_pin: ^PB12
# driver_IHOLDDELAY: 8
# driver_TPOWERDOWN: 20
# driver_TBL: 1
# driver_TOFF: 1
# driver_HEND: 0
# driver_HSTRT: 7
driver_SGTHRS: 75 # меняем на 65 если не меняли шкивы и 105 если только шкивы меняли

[stepper_y]
step_pin: PB8
dir_pin: !PB7
enable_pin: !PC3
microsteps: 32
rotation_distance: 40 # меняем на 72 если не меняли шкивы
endstop_pin: tmc2209_stepper_y:virtual_endstop
position_endstop: -0.5
position_min: -0.5
position_max: 226
homing_speed: 36
homing_retract_dist:0

[tmc2209 stepper_y]
uart_pin:PA10
interpolate: True
run_current:1.5
hold_current:1.0
sense_resistor: 0.100
stealthchop_threshold: 0
uart_address:3
diag_pin: ^PB13
# driver_IHOLDDELAY: 8
# driver_TPOWERDOWN: 20
# driver_TBL: 1
# driver_TOFF: 1
# driver_HEND: 0
# driver_HSTRT: 7
driver_SGTHRS: 75 # меняем на 65 если не меняли шкивы и 105 если только шкивы меняли

[stepper_z]
step_pin: PB6
dir_pin: !PB5
enable_pin: !PC3
microsteps: 16
rotation_distance:8
gear_ratio: 64:20
endstop_pin: tmc2209_stepper_z:virtual_endstop# PA15   #probe:z_virtual_endstop
position_endstop: 0
position_max: 255
position_min: -5

[tmc2209 stepper_z]
uart_pin: PA11
uart_address: 3
run_current: 0.8
diag_pin: ^PB14
stealthchop_threshold: 0
sense_resistor: 0.100
# driver_IHOLDDELAY: 8
# driver_TPOWERDOWN: 20
# driver_TBL: 1
# driver_TOFF: 1
# driver_HEND: 2
# driver_HSTRT: 2
driver_SGTHRS: 0

[extruder]
max_extrude_only_distance: 1000.0
max_extrude_cross_section: 80
step_pin: nozzle_mcu:PB1
dir_pin: nozzle_mcu:PB0
enable_pin: !nozzle_mcu:PB2
microsteps: 16
rotation_distance: 6.9 # тут меняем  на свой шаг после проверки на шаги экструдера
nozzle_diameter: 0.400
filament_diameter: 1.750
heater_pin: nozzle_mcu:PB7
sensor_type: EPCOS 100K B57560G104F
sensor_pin: nozzle_mcu:PA0
pressure_advance: 0.04
pressure_advance_smooth_time: 0.040
#control: pid
#pid_Kp: 25.013
#pid_Ki: 2.566
#pid_Kd: 60.966
min_temp: 0
max_temp: 320

[tmc2209 extruder]
uart_pin: nozzle_mcu:PB11
tx_pin: nozzle_mcu:PB10
uart_address: 3
run_current: 0.5 # тут снижаем ток  если греется эсктрудер если сильно снизить может начать пропускать шаги рекомендуемый диапазон от 0.45 до 0.55
sense_resistor: 0.150
stealthchop_threshold: 0
# driver_IHOLDDELAY: 8
# driver_TPOWERDOWN: 20
# driver_TBL: 2
# driver_TOFF: 3
# driver_HEND: 0
# driver_HSTRT: 5

[heater_bed]
heater_pin: PB10
sensor_type: EPCOS 100K B57560G104F
sensor_pin: PC4
control: watermark
# control: pid
# pid_kp: 27
# pid_ki: 0.08
# pid_kd: 0
min_temp: 0
max_temp: 115 # из файла можно послать максимальную температуру -15 от тут указанной, тоесть чтобы спокойно посылать из орки 115 здесть лучше указать 130 а надежнее 135

[filament_switch_sensor filament_sensor]
pause_on_runout: true
switch_pin: !PC15
runout_gcode:
  {% if printer.extruder.can_extrude|lower == 'true' %}
    G91
    G0 E30 F600
    G90
  {% endif %}
  beep # звуковой сигнал если заканчивается филамент во время печати 
  beep # два раза чтобы было 2 пика для отличия от сигнала в конце печати

[filament_switch_sensor filament_sensor_2]
pause_on_runout: true
switch_pin: !nozzle_mcu:PA10

[multi_pin heater_fans]
pins:nozzle_mcu:PB5,PB2

[heater_fan hotend_fan]
pin: multi_pin:heater_fans
heater: extruder
heater_temp: 40

[static_digital_output my_fan_output_pins]
pins: nozzle_mcu: PB6

[output_pin fan0]
pin: !nozzle_mcu: PB8
pwm: True
cycle_time: 0.0100
hardware_pwm: false
value: 0.00
scale: 255
shutdown_value: 0.0

[output_pin fan1]
pin: PC0
pwm: True
cycle_time: 0.0100
hardware_pwm: false
value: 0.00
scale: 255
shutdown_value: 0.0

[output_pin fan2]
pin: PB1
pwm: True
cycle_time: 0.0100
hardware_pwm: false
value: 0.00
scale: 255
shutdown_value: 0.0

[output_pin LED]
pin:PB0
pwm: True
cycle_time: 0.010
value: 1

[adxl345]
cs_pin: nozzle_mcu:PA4
spi_speed: 5000000
axes_map: x,-z,y
spi_software_sclk_pin: nozzle_mcu:PA5
spi_software_mosi_pin: nozzle_mcu:PA7
spi_software_miso_pin: nozzle_mcu:PA6

[resonance_tester]
accel_chip: adxl345
accel_per_hz: 75
# min_freq: 30
# max_freq: 100
probe_points:
   110,110,10

[prtouch_v2]  # K1
pr_version: 1
step_base: 2
z_offset: 0 
noz_ex_com: 0.05
tilt_corr_dis: 0.03
tri_min_hold: 2000
tri_max_hold: 6000
pres_cnt: 4
pres0_clk_pins: leveling_mcu:PA5
pres0_sdo_pins: leveling_mcu:PA1
pres1_clk_pins: leveling_mcu:PA2
pres1_sdo_pins: leveling_mcu:PA0
pres2_clk_pins: leveling_mcu:PA6
pres2_sdo_pins: leveling_mcu:PA3
pres3_clk_pins: leveling_mcu:PA7
pres3_sdo_pins: leveling_mcu:PA4
show_msg: False
step_swap_pin: PC10
pres_swap_pin: leveling_mcu:PB1
g28_wait_cool_down: true
pa_clr_down_mm: -0.15
clr_noz_start_x: 95
clr_noz_start_y: 221
clr_noz_len_x: 40
clr_noz_len_y: 2
speeds: 2.5,1.0
tri_hftr_cut: 2,1
tri_lftr_k1: 0.70,0.30
tri_try_max_times: 10
tri_min_hold: 2000,20000
tri_max_hold: 6000,60000

[bed_mesh]
speed: 150
mesh_min: 5,5
mesh_max: 215,215
probe_count: 5,5
fade_start: 1.0 # начало компенсации слоев. если не ровняли стол и перепад больше 1 мм может давать ошибку при большой площади печати
fade_end: 10.0 # конец компенсации слоев 

[display_status]

[printer]
kinematics: corexy
max_velocity: 800
max_accel: 20000
max_accel_to_decel: 20000
max_z_velocity: 20
square_corner_velocity: 5.0
square_corner_max_velocity: 200.0
max_z_accel: 300

[pause_resume]
# recover_velocity: 500.

[exclude_object]

#*# <---------------------- SAVE_CONFIG ---------------------->
#*# DO NOT EDIT THIS BLOCK OR BELOW. The contents are auto-generated.
#*#
#*# [bed_mesh default]
#*# version = 1
#*# points =
#*# 	0.241040, 0.191540, 0.251196, 0.340134, 0.481821
#*# 	0.030081, 0.054321, 0.086415, 0.169352, 0.221602
#*# 	-0.027064, -0.021648, 0.050000, 0.084759, 0.115384
#*# 	-0.066200, -0.041210, 0.025915, 0.002571, 0.091415
#*# 	-0.077991, -0.080616, -0.013929, 0.010634, 0.091474
#*# x_count = 5
#*# y_count = 5
#*# mesh_x_pps = 2
#*# mesh_y_pps = 2
#*# algo = lagrange
#*# tension = 0.2
#*# min_x = 5.0
#*# max_x = 215.0
#*# min_y = 5.0
#*# max_y = 215.0
#*#
#*# [extruder]
#*# control = pid
#*# pid_kp = 31.440
#*# pid_ki = 3.882
#*# pid_kd = 63.665
#*#
#*# [input_shaper]
#*# shaper_type_x = mzv
#*# shaper_freq_x = 59.2
#*# shaper_type_y = zv
#*# shaper_freq_y = 60.4

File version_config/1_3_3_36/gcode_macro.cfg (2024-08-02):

# K1
# CreateDate: 2023/03/21

[gcode_macro PRINTER_PARAM]
variable_z_safe_pause: 0.0
variable_z_safe_g28: 3.0
variable_max_x_position: 220.0
variable_max_y_position: 220.0
variable_max_z_position: 250.0
variable_fans: 3
variable_auto_g29: 0
variable_fan0_min: 25
variable_fan1_min: 50
variable_fan2_min: 180
variable_fan2_speed: 0
variable_hotend_temp: 0
variable_e_min_current: 0.27
variable_cam_off_temp: 60
gcode:

[gcode_macro AUTOTUNE_SHAPERS]
#variable_autotune_shapers: 'ei'
gcode:

[gcode_macro LOAD_MATERIAL_CLOSE_FAN2]
variable_fan2_value: 0
gcode:
  SAVE_GCODE_STATE NAME=myMoveState
  {% if printer['output_pin fan2'].value > 0.0 %}
    SET_GCODE_VARIABLE MACRO=LOAD_MATERIAL_CLOSE_FAN2 VARIABLE=fan2_value VALUE={printer['output_pin fan2'].value}
    M107 P2
  {% endif %}
  RESTORE_E_CURRENT

[gcode_macro LOAD_MATERIAL_RESTORE_FAN2]
gcode:
  {% set fan2_value = printer['gcode_macro LOAD_MATERIAL_CLOSE_FAN2'].fan2_value|float %}
  RESTORE_GCODE_STATE NAME=myMoveState
  {% if fan2_value > 0.0 %}
    {% set s_value = (fan2_value * 255 - printer["gcode_macro PRINTER_PARAM"].fan2_min) * 255 / (255 - printer["gcode_macro PRINTER_PARAM"].fan2_min) %}
    M106 P2 S{s_value}
    SET_GCODE_VARIABLE MACRO=LOAD_MATERIAL_CLOSE_FAN2 VARIABLE=fan2_value VALUE=0
  {% endif %}
  SET_E_MIN_CURRENT

[gcode_macro SET_E_MIN_CURRENT]
gcode:
  {% set e_current = printer['gcode_macro PRINTER_PARAM'].e_min_current %}
  M400
  SET_TMC_CURRENT STEPPER=extruder CURRENT={e_current} HOLDCURRENT={e_current}
  G4 P2000

[gcode_macro RESTORE_E_CURRENT]
gcode:
  {% set e_current = printer.configfile.settings['tmc2209 extruder'].run_current %}
  M400
  SET_TMC_CURRENT STEPPER=extruder CURRENT={e_current} HOLDCURRENT={e_current}
  G4 P2000

[gcode_macro LOAD_MATERIAL]
gcode:
  LOAD_MATERIAL_CLOSE_FAN2
  M109 S{printer.custom_macro.default_extruder_temp}
  G91
  G1 E80 F180
  LOAD_MATERIAL_RESTORE_FAN2

[gcode_macro QUIT_MATERIAL]
gcode:
  SAVE_GCODE_STATE NAME=myMoveState
  RESTORE_E_CURRENT
  M109 S{printer.custom_macro.default_extruder_temp}
  M83
  G1 E100 F300
  G1 E-15 F3000
  G1 E-22.4700 F2400
  G1 E-6.4200 F1200
  G1 E-3.2100 F720
  G1 E5.0000 F356
  G1 E-5.0000 F384
  G1 E5.0000 F412
  G1 E-5.0000 F440
  G1 E5.0000 F467
  G1 E-5.0000 F495
  G1 E5.0000 F523
  G1 E-5.0000 F3000
  G1 E-15 F3000
  SET_E_MIN_CURRENT
  RESTORE_GCODE_STATE NAME=myMoveState
  
[gcode_macro Qmode]
variable_flag: 0
variable_accel: 0
variable_accel_to_decel: 0
variable_velocity: 0
variable_square_corner_velocity: 0
variable_pressure_advance:0.0
variable_fan0_value: 0.00
variable_fan1_value: 0.00
variable_fan2_value: 0.00
variable_speed_factor: 0
variable_max_accel: 2500
variable_max_accel_to_decel: 2500
gcode:
  {% set printer_state = printer.print_stats.state %}
  {% if printer['gcode_macro Qmode'].flag|int == 0 %}
    {% if printer_state == "printing" or printer_state == "paused" %}
      SET_GCODE_VARIABLE MACRO=Qmode VARIABLE=accel VALUE={printer.toolhead.max_accel}
      SET_GCODE_VARIABLE MACRO=Qmode VARIABLE=accel_to_decel VALUE={printer.toolhead.max_accel_to_decel}
      SET_GCODE_VARIABLE MACRO=Qmode VARIABLE=velocity VALUE={printer.toolhead.max_velocity}
      SET_GCODE_VARIABLE MACRO=Qmode VARIABLE=square_corner_velocity VALUE={printer.toolhead.square_corner_velocity}
      SET_GCODE_VARIABLE MACRO=Qmode VARIABLE=pressure_advance VALUE={printer.extruder.pressure_advance}
      SET_GCODE_VARIABLE MACRO=Qmode VARIABLE=speed_factor VALUE={printer.gcode_move.speed_factor}
      SET_TMC_FIELD STEPPER=stepper_x FIELD=en_spreadcycle VALUE=0
      SET_TMC_FIELD STEPPER=stepper_y FIELD=en_spreadcycle VALUE=0
      SET_TMC_CURRENT STEPPER=stepper_x CURRENT=1.0
      SET_TMC_CURRENT STEPPER=stepper_y CURRENT=1.0
      G4 P1000

      # Set Motion Parameters
      SET_VELOCITY_LIMIT ACCEL=2500
      SET_VELOCITY_LIMIT ACCEL_TO_DECEL=2500
      SET_VELOCITY_LIMIT VELOCITY=150
      SET_VELOCITY_LIMIT SQUARE_CORNER_VELOCITY=5
      SET_PRESSURE_ADVANCE ADVANCE=0.05
      M220 S50

      {% set tmp = printer['output_pin fan0'].value * 255 %}
      SET_GCODE_VARIABLE MACRO=Qmode VARIABLE=fan0_value VALUE={tmp}
      {% if tmp - printer['gcode_macro PRINTER_PARAM'].fan0_min > (255 - printer['gcode_macro PRINTER_PARAM'].fan0_min) / 2 %}
        {% set tmp = printer['gcode_macro PRINTER_PARAM'].fan0_min + (255 - printer['gcode_macro PRINTER_PARAM'].fan0_min) / 2 %}
        SET_PIN PIN=fan0 VALUE={tmp}
      {% endif %}

      {% set tmp = printer['output_pin fan1'].value * 255 %}
      SET_GCODE_VARIABLE MACRO=Qmode VARIABLE=fan1_value VALUE={printer['output_pin fan1'].value * 255}
      {% if tmp - printer['gcode_macro PRINTER_PARAM'].fan1_min > (255 - printer['gcode_macro PRINTER_PARAM'].fan1_min) / 2 %}
        {% set tmp = printer['gcode_macro PRINTER_PARAM'].fan1_min + (255 - printer['gcode_macro PRINTER_PARAM'].fan1_min) / 2 %}
        SET_PIN PIN=fan1 VALUE={tmp}
      {% endif %}

      {% set tmp = printer['output_pin fan2'].value * 255 %}
      SET_GCODE_VARIABLE MACRO=Qmode VARIABLE=fan2_value VALUE={printer['output_pin fan2'].value * 255}
      {% if tmp - printer['gcode_macro PRINTER_PARAM'].fan2_min > (255 - printer['gcode_macro PRINTER_PARAM'].fan2_min) / 2 %}
        {% set tmp = printer['gcode_macro PRINTER_PARAM'].fan2_min + (255 - printer['gcode_macro PRINTER_PARAM'].fan2_min) / 2 %}
        SET_PIN PIN=fan2 VALUE={tmp}
      {% endif %}

      SET_GCODE_VARIABLE MACRO=Qmode VARIABLE=flag VALUE=1
      SET_QMODE_FLAG FLAG=1
    {% endif %}
  {% endif %}

[gcode_macro Qmode_exit]
gcode:
  {% set printer_state = printer.print_stats.state %}
  {% if printer['gcode_macro Qmode'].flag|int == 1 %}
    {% if printer_state == "printing" or printer_state == "paused" %}
      SET_VELOCITY_LIMIT ACCEL={printer['gcode_macro Qmode'].accel}
      SET_VELOCITY_LIMIT ACCEL_TO_DECEL={printer['gcode_macro Qmode'].accel_to_decel}
      SET_VELOCITY_LIMIT VELOCITY={printer['gcode_macro Qmode'].velocity}
      SET_VELOCITY_LIMIT SQUARE_CORNER_VELOCITY={printer['gcode_macro Qmode'].square_corner_velocity}
      SET_PRESSURE_ADVANCE ADVANCE={printer['gcode_macro Qmode'].pressure_advance}
      M220 S{printer['gcode_macro Qmode'].speed_factor * 100}

      {% set X_RUN_CUR = printer.configfile.settings['tmc2209 stepper_x'].run_current %}
      {% set Y_RUN_CUR = printer.configfile.settings['tmc2209 stepper_y'].run_current %}
      SET_TMC_CURRENT STEPPER=stepper_x CURRENT={X_RUN_CUR}
      SET_TMC_CURRENT STEPPER=stepper_y CURRENT={Y_RUN_CUR}
      SET_TMC_FIELD STEPPER=stepper_x FIELD=en_spreadcycle VALUE=1
      SET_TMC_FIELD STEPPER=stepper_y FIELD=en_spreadcycle VALUE=1
      G4 P1000

      {% if printer['output_pin fan0'].value != 0 %}
        {action_respond_info("fan0_value = %s" % printer['gcode_macro Qmode'].fan0_value)}
        SET_PIN PIN=fan0 VALUE={printer['gcode_macro Qmode'].fan0_value}
        SET_GCODE_VARIABLE MACRO=Qmode VARIABLE=fan0_value VALUE=0
      {% endif %}
      {% if printer['output_pin fan1'].value != 0 %}
        {action_respond_info("fan1_value = %s" % printer['gcode_macro Qmode'].fan1_value)}
        SET_PIN PIN=fan1 VALUE={printer['gcode_macro Qmode'].fan1_value}
        SET_GCODE_VARIABLE MACRO=Qmode VARIABLE=fan1_value VALUE=0
      {% endif %}
      {% if printer['output_pin fan2'].value != 0 %}
        {action_respond_info("fan2_value = %s" % printer['gcode_macro Qmode'].fan2_value)}
        SET_PIN PIN=fan2 VALUE={printer['gcode_macro Qmode'].fan2_value}
        SET_GCODE_VARIABLE MACRO=Qmode VARIABLE=fan2_value VALUE=0
      {% endif %}

      SET_GCODE_VARIABLE MACRO=Qmode VARIABLE=flag VALUE=0
      SET_QMODE_FLAG FLAG=0
    {% endif %}
  {% endif %}

[gcode_macro M204]
rename_existing: M204.1
gcode:
  # {% if printer['gcode_macro Qmode'].flag|int == 0 %}
    {% set get_params = "" %}
    {% set qmode_max_accel = printer['gcode_macro Qmode'].max_accel|string %}
    {% if 'S' in params|upper %}
      {% if printer['gcode_macro Qmode'].flag|int == 1 and params.S|float > qmode_max_accel|float %}
        {% set get_params = (get_params + ' ' + 'S' + qmode_max_accel) %}
      {% else %}
        {% set get_params = (get_params + ' ' + 'S' + params.S) %}
      {% endif %}
    {% endif %}
    {% if 'P' in params|upper %}
      {% if printer['gcode_macro Qmode'].flag|int == 1 and params.P|float > qmode_max_accel|float %}
        {% set get_params = (get_params + ' ' + 'P' + qmode_max_accel) %}
      {% else %}
        {% set get_params = (get_params + ' ' + 'P' + params.P) %}
      {% endif %}
    {% endif %}
    {% if 'T' in params|upper %}
      {% if printer['gcode_macro Qmode'].flag|int == 1 and params.T|float > qmode_max_accel|float %}
        {% set get_params = (get_params + ' ' + 'T' + qmode_max_accel) %}
      {% else %}
        {% set get_params = (get_params + ' ' + 'T' + params.T) %}
      {% endif %}
    {% endif %}
    M204.1 {get_params}
  # {% endif %}
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

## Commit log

2023-06-30 Update readme.md
    правки
2023-06-30 Update readme.md
    ссылка на плату
2023-06-30 Add files via upload
    фото платы
2023-06-30 Update readme.md
    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
2023-07-01 исходные файлы
    [gcode_macro.cfg, printer.cfg, printer_params.cfg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]
2023-07-04 экстендер крышки
2023-07-04 спейсер добавил
2023-07-04 меню высот стола
2023-07-31 Rename gcode_macro (2).cfg to gcode_macro.cfg
    [gcode_macro.cfg]
2023-08-06 реорганизация
    [gcode_macro.cfg, printer.cfg, printer_params.cfg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]
2023-09-17 filament change
    [filament.cfg, gcode_macro.cfg]
2023-09-17 спасибо добавил
2023-09-17 filament macros
2023-09-17 замена картинки
2023-09-17 ребут в конце правок
2023-09-19 бутлоадер
2023-09-28 макрос отсчета поменял
    [filament.cfg]
2023-09-28 фикс мароса
    [filament.cfg]
2023-12-06 отлаженная версия
    [Adaptive_Meshing.cfg, KAMP_Settings.cfg, Line_Purge.cfg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]
2023-12-06 конфиги для к1 сток
2023-12-06 спасибо автору
2023-12-17 шейпер скрипт прогресс
2023-12-17 прогресс
2023-12-17 тар временный
2023-12-17 временный
2023-12-17 проверка
2023-12-17 каменный цветок
2023-12-17 бьемся лбом
2023-12-17 идеи кончились.
2023-12-17 ну вроде нашел
2023-12-17 нифига
2023-12-17 релоад
    [shape.cfg]
2023-12-17 описание
2023-12-17 полировка
2023-12-24 правильная дата в принтере
2023-12-24 правильное время
2023-12-24 орфография, беспощадная ты сука...
2023-12-24 справочная информация
2023-12-24 табличку добавил
2023-12-24 правки не работает кода пока
2023-12-30 нет спасибо
2024-01-13 retract add
    [printer.cfg]
2024-01-28 прошивка 1_3_3_5
    [Adaptive_Meshing.cfg, KAMP_Settings.cfg, Line_Purge.cfg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]
2024-01-28 добавил порядок установки и архув для макса
2024-01-28 добавки описания
2024-01-28 спасибо
2024-02-04 поправил ссылку
2024-02-10 таймер отложенной печати
2024-02-11 таймер
2024-02-11 мануал по таймеру.
2024-02-11 новая версия скрипта
2024-02-15 теперь работает
2024-03-15 апдейт
2024-05-03 обнова
2024-05-13 орфография
2024-05-26 орфография, беспощадная ты сука
2024-05-26 дополнения
2024-06-22 правим
2024-06-23 попытка 2
    [Cube.stl]
2024-06-23 правки33
2024-06-23 орфография меня доконает
2024-06-23 релиз
2024-07-15 обновил всякое
    [Adaptive_Meshing.cfg, KAMP_Settings.cfg, Line_Purge.cfg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]
2024-07-15 правка кода
2024-07-15 ссылку на гладиолуча поправил
2024-07-18 бета
2024-08-29 добавил пару пунктов меню
2024-08-29 правка меню гита
2024-08-29 добавочка
2024-08-29 ссылка на "чай"
2024-08-29 добавил корпус
2024-08-29 пояснения
2024-08-29 добавочки
2024-08-29 дополнение
2024-09-17 в процессе правок
2024-10-09 распиновка
2024-10-09 обновления текстов
2024-10-09 очепятка
2024-10-09 пояснялки к пунктам меню.
2024-10-09 доработки
2024-10-12 дополнениния
2024-10-14 очепятки
2024-10-14 тензомод
2024-10-16 Калибровка точности по Соркину
2024-11-02 добавка про температуру стола
    [printer.cfg]
2024-12-04 правки.
2024-12-04 Подключение нагревателя камеры принтера
2024-12-04 послесловие
2024-12-05 ссылки на модели
2024-12-09 добавка к1се
2024-12-10 исправление
2024-12-11 исправление скрипта.
2024-12-11 обновление.
2025-01-18 ссылка на пеи
2025-01-19 pi screen конфиг
2025-02-07 соркин о настройках
2025-05-26 мануалы термокамеры
2025-05-27 hotend k2
2025-06-01 новые товары
2025-06-10 изменения скрипта
2025-06-20 3002 ошибка
